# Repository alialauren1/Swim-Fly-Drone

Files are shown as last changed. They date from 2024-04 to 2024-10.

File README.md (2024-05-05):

# Swim Fly Drone Project

Our project entails constructing a submersible chamber capable of reaching
specified depths. The system will operate in a closed loop, maintaining control until it 
reaches a desired pressure depth.

This project was intended for our senior project where. Dr. Ghalamchi wants to improve previous tests on waterproof drones that can take off from underwater to allow for a drone that can float on top of the water surface as well as have added support to be pushed up from underwater. The new design needs to be detachable from the built waterproof drone to compare its new features in tests. The propellers must also be above the water surface when the drone is idling on the water so that the efficiency of takeoff can be compared to the drone without the chamber in which the whole drone is submerged underwater upon takeoff.

Our project for ME 405 will be the system attached to this drone, enabling the drone to submerge underwater with a minimum depth of 5ft. While allowing for the system to resurface and position the propellers above the water's surface. 

Pressure can be directly correlated to depth, given a liquid's density.
   In order to simulate this system for our ME 405 Term Project, this system takes a desired pressure setpoint and controls a motor-driven syringe system to
   pressurize a chamber to the setpoint. It waits a period of time, as if it were underwater collecting data,
   and then returns to the initial pressure, as if it were returning to the water surface. 

## Hardware design
In Figure 1, we can see the internal system of the system. We have integrated Ametck Pittman's PG6712A077-R3 motor to a 50 CC syringe. Utilizing this motor, we've have attached a worm gear and gears to ensure sufficient torque to be generated. These gears are attached to a pinion
and aligned with a rack that allows for the syringe to be moved back and forth. This allows
for the system to achieve the desired weight to submerge the whole system.

The gears were selected from McMaster. This is so in the future, they can be ordered parts. For now, we used the CAD files to 3D print them for budget reasons. While sizing and choosing the number of teeth we would need for our system, we calculated to torque that the motor needed to have to overcome the friction force between the piston and syringe. This calculation is shown below. In the future, we can order a motor that is more selectively chosen using this information. However for now, we used the motor provided to us in lab. 

$F_r = T_A / R_A$

$T_A = F_R * R_A$

$T_B = T_A$

$T_C = (N_C / N_B ) * T_B$

$T_C = (N_C / N_B ) * (F_R * R_A)$

$T_C = (1/15) * (6 N) * (.0152 m)$

$T_C = (0.006 Nm) = (6 mNm)$ 

Doing these calculations led us to select appropriate gears for our system, ensuring that they can withstand the pressure encountered during operation while maintaining an ideal speed. Below shows a table of the parameters.  

| **Parameters** | Variable | Value | Units |
|:---:|:---:|:---:|:---:|
| **----Rack+Piston+Syringe--** |  **-------** |  **----** |  **----** |
| Force to overcome friction in tube | F_R | 6 | N |
| **----Gears--** |  **-------** | **-----** | **-----** |
| Radius Gear A | R_A | 0.0152  | m |
| Teeth Gear A | N_A | 17 | |
| Outer Diameter Worm Gear B | OD_B | 16 | mm |
| Teeth Worm Gear B | N_B | 15 | |
| Pressure Angle Worm Gear B | Phi_C | 20 |  degrees  |
| Outer Diameter Worm C | OD_C | 12 | mm |
| Pressure Angle Worm C | Phi_C | 20 |  degrees  |
| Teeth Worm C | N_C | 1 | |
| **-----Motor Parameters------**  | **--------** | **-----** |  **----** |
| Radius of Motor Gear | rm |  0.00662  | m |
| Motor Nominal Voltage | V_DC | 12 | V |



Figure 1. CAD: Internal system of our terms project with labels indicating parts of the system.



Figure 2. CAD: Secondary view of the internal system of our terms project with labels indicating parts of the system.

Screenshot 2024-03-19 at 6 15 07 PM

Figure 3. Gears, motor, and frame for the internal system.

The pressure sensor we selected is the SSCMANV030PA2A3 Honeywell Pressure Sensor. It measures absolute pressure, with a range from 0-30 psi. Is allows liquid media on the port, which will come of use in future quarters when we test our system underwater. 

Screenshot 2024-03-19 at 8 53 00 PM

Figure 4. SSCMANV030PA2A3 Honeywell Pressure Sensor



Figure 5. Hardware all connected



Figure 6A. System Connected to Bottom of Drone Body - View 1



Figure 6B. System Connected to Bottom of Drone Body - View 2

Screenshot 2024-03-19 at 8 43 37 PM

Figure 7. Overall View of Drone Body with Chamber 

### Schematic

The schematic below shows a very general diagram of how components are being powered and communicating with one another. 
The power supply provides power to the motor. The power supply was set to 12V with a 0.5 A current limit. 

Schematic

Figure 8. Schematic of components

## Software design
The main program uses three classes inside two tasks that multitask with one another. A detailed description of the software design can be found on our doxygen main page linked here: 
https://alialauren1.github.io/ME405-Term-Project/index.html#soft_org_sec

To measure pressure, we used a Honeywell Board Mount Pressure Sensor, which uses I^2C communication. A class was made to use this sensor. Details on how the data was collected and process is linked below. Pressure Sensor: SSCMANV030PA2A3
https://alialauren1.github.io/ME405-Term-Project/index.html#autotoc_md1

Attaching the sensor and the Ametek motor to our Nucleo, we were able to program both components to get a functioning product.

### Tasks and States
The Tasks and States used in the main program are shown in diagrams linked on the page below.
https://alialauren1.github.io/ME405-Term-Project/index.html#T_S_sec

## Testing and Results

### Preliminary
Our senior project requires our chamber to be able to acheive at minimum, 5 ft depth. Calculations were run, shown below, to determine the pressure that coincides with a depth of 5 ft in water. Being a little under 16.5 psi, we decided to run initial tests at 16.5 psi.

Screenshot 2024-03-19 at 9 05 30 PM

In order to test our project sensors and motor control, we ran multiple tests in order to find our optimal Kp value. The results are presented in the plot down below. This was preliminary testing. 

Screenshot 2024-03-17 at 10 32 32 PM

Figure 9. Plot of Pressure vs Time inside the syringe. Each line represents a different run of data collected while altering the Kp value.

During our testing, we initially set Kp to 5 (shown in blue) and then increased it to 10 (shown in orange). Observing the graph, it's evident that increasing the Kp value led to faster attainment of the target pressure of 16.5 [psi].

While testing to achieve for efficiency in reaching the desired pressure, it's essential to consider what our system will be attached to. Our system with the syringe and pressure sensor will be attached to a drone. Rapid pressure and volume changes may introduce a moment within the drone body, causing the drone to loose control. Therefore, we must weigh the trade-offs between achieving rapid pressure targets and maintaining system stability.

As we continue to test our project, further tests will be necessary to determine the optimal balance between speed, the system stability and accuracy. This process may involve fine-tuning parameters beyond just changing the Kp. This may incude making the chamber of the system bigger and other factors.

### Lab Demo Results and Functionality of Product
The below plot shows the pressure inside the syringe. The autonomous journey is one in which the system reaches the desired setpoint, waits for a duration, and then returns to the initial pressure. 



Figure 10. Plot of Pressure vs Time inside the syringe with a setpoint of 17 [psi].  

This journey mimics future developement of our larger senior project in which this pressure chamber will be attached to a drone. We anticipate it will be beneficial for some remote or signal to send a desired depth as the setpoint to the system, in which the chamber will submerge with the drone, going to that depth. It will remain there, possible to collect data, and then autonomously return to the surface. 
We are satisfied with the final results. The chamber is able to reach pressures higher than a pressure corresponding to 5ft, which was what we wanted to achieve.
It is also able to maintain the increase in pressure while the motor is turned off, which is a satisfying result. 

The system also works at lower than atmosphere pressures. In the plot below, the setpoint was chosen as 13 psi. However, in another test, we were able run the system with an even lower setpoint of 10 psi. Although this is less necessary to have, it is satisfying to see that ability. 

Screenshot 2024-03-19 at 8 38 33 PM

Figure 11. Plot of Pressure vs Time inside the syringe with a setpoint of 13 [psi].  

## What we have learned
Designing this system taught us how important it is to design and test early. 
Although most of the system was done with a reasonable amount of time, we were faced with issues causing the system to take longer to complete than anticipated.

### 3D Printing
While 3D printing gears and housing system for our project we learned that tolerances while creating parts is harder to achieve. When 3D printing the gears it was harder to align the gears causing the small gears to slip and not allowing for our system to be as efficient as it can be.

Note: We are saving our used PLA parts to find a place to recycle them. 

Screenshot 2024-03-19 at 6 14 47 PM

Figure 12. Collection of gears tested

### Software and Sensors
We learned that the data being output from our pressure sensor was in counts. This led to the creation of a definition in our PressureSensor class to interpret the counts into a unit of measurement that could be easily interpretted, that being [psi]. Since our Closed-Loop Controller class uses the pressure sensor output in counts to correct for a desired pressure, an additional definition was made to interpret user desired setpoint input from [psi] to counts. 

## Safety
Our project prioritizes user safety through thoughtful design considerations. By utilizing small gears, we have effectively reduced the risk of injuries to the user. Once the system has been fully assembled, all moving components and electrical elements will be enclosed and inaccessible to the user. This design ensures that users are protected from potential hazards during the system's operation.

## Bugs and Future Work

We would also like to fix our code in Task2 State 3 where there is a break in data collection between the chamber resting at a higher pressure and then returning to its original pressure. As shown on the plot in the "Lab Demo Results" section, there is a small duration of time in which no data is collected. That is state 3, whilst counter_s3 is between 1 and 3. We tried removing this portion and only having state 3 reset the setpoint to initial pressure in one count but it did not initially work and we have run out of time to work on the code. So, for now, there is that small time duration blip in the data.  

In the future we would like to implement a third task into our main program that is a user interface for the pressure setpoint. 
The user could select from a range of setpoint options and the system would adjust the pressure in the chamber accordingly. 
This task would multitask with the other two tasks and allow for the user to input a setpoint whenever they want whilst the program runs. 

We plan to build a larger waterproof chamber to encompass components similar to those used in project. This will allows us to test the systems depth control abilities in actual water. We look forward to the continuation of this project and appreciate all that it has taught us so far. 

## Additional files

Pressure sensor datasheet:
[SSCMANV030PA2A3 Honeywell.pdf](https://github.com/alialauren1/ME405-Term-Project/files/14630972/SSCMANV030PA2A3.Honeywell.pdf)

I2C Communications with Honeywell Pressure Sensors:
[sps-siot-i2c-comms-digital-output-pressure-sensors-tn-008201-3-en-ciid-45841.pdf](https://github.com/alialauren1/ME405-Term-Project/files/14630975/sps-siot-i2c-comms-digital-output-pressure-sensors-tn-008201-3-en-ciid-45841.pdf)

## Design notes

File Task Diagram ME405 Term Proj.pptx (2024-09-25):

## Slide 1

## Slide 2

Initial Pressure
Bytes

Task 1 Print
Freq: 60 Hz
Priority: 1

Task 2 Get
Freq: 50 Hz
Priority: 2

Time and Pressure Bytes [100]

Task 2 State Status
Byte

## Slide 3

Task 2 Get

Start

setpoint_raw-6 <= reader_p_value <= setpoint_raw+6

counter_s3 == 4

State 2 Off
Collect Data whilst Motor Off

State 3 Go Back
Reset Setpoint to Initial Pressure

Always

State 1 Data
Collect Data and Run CL Controller

State 4 Nothing
Does nothing

counter == 20

(initialP-6 <= reader_p_value <= initialP+6)
& key == 1

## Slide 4

T2_state == 3

Task 1 Print

Start

T2_state == 1

State 2
No Values, Don’t Print

Always

State 1 Print
Print Values

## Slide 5

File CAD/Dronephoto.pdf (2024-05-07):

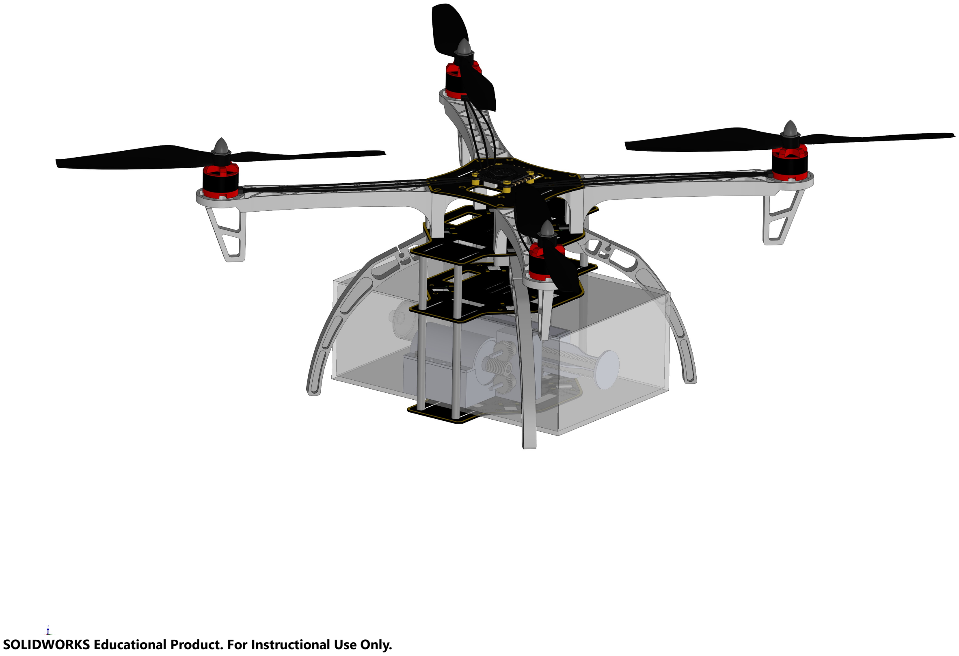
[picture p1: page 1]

SOLIDWORKS Educational Product. For Instructional Use Only.

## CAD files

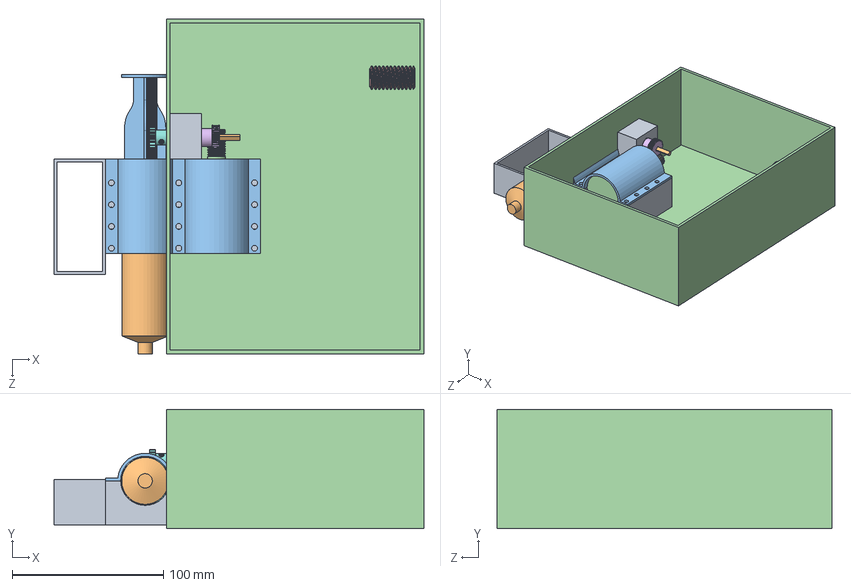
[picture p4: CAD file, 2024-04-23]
Pelican Paddler CAD/BuoyancyChamberAssembly_RevA.SLDASM
244.4 x 78.7 x 221.0 mm
ComponentStucture
60mlSyringeShell
60mlSyringePlunger
Motor_body
57545K736_Metal Worm Gear x 2
57545K624_Steel Worm
2664N437_Metal Gear - 20 Degree Pressure Angle x 2
2485N214_Metal Gear Rack - 20 Degree Pressure Angle x 2
6mm bar x 2

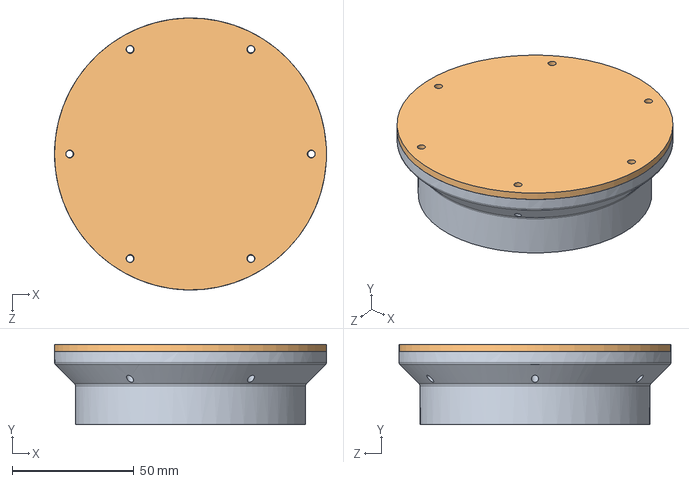
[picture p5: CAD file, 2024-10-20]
CAD/Housing/Housing Part Files/TestBox_LidSeal_v1.SLDASM
111.9 x 33.0 x 111.9 mm
TestBox_LidSeal_v1
TestBox_Lid_v1

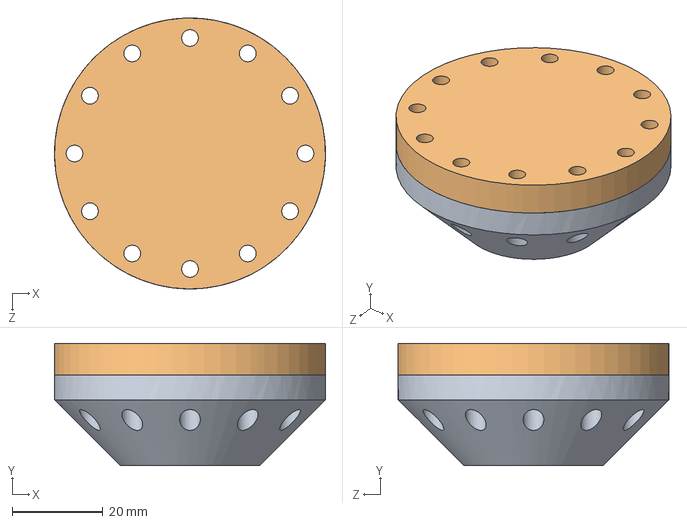
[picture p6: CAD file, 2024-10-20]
CAD/Housing/Housing Part Files/Lid Assembly.SLDASM
59.8 x 27.0 x 59.8 mm
TestBox_LidSeal_v1
Part1^Lid Assembly

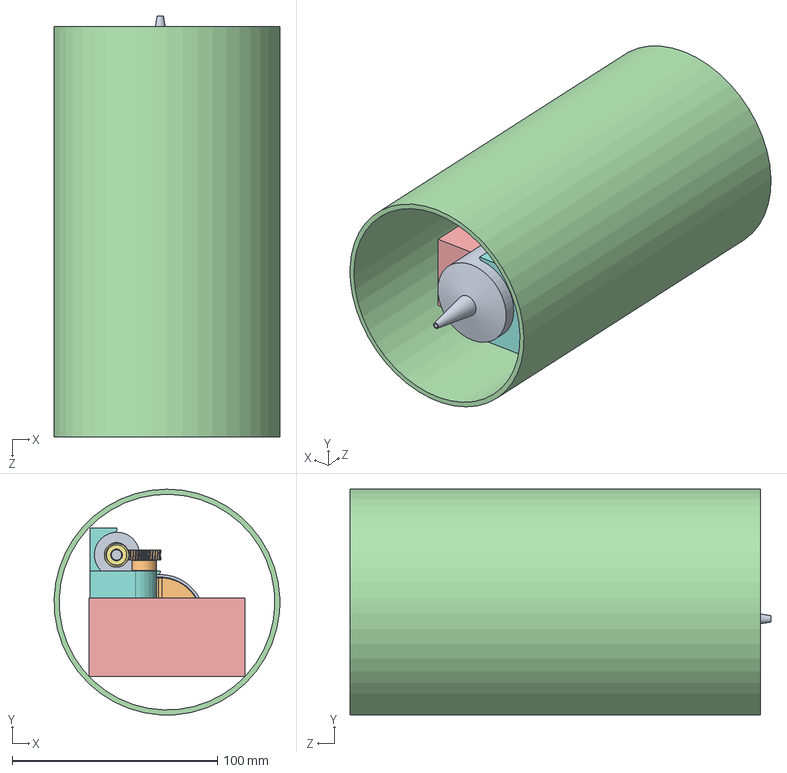
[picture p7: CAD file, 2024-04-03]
CAD/CAD_ME405/syring_1_V3.SLDASM
109.9 x 109.9 x 205.0 mm
syringe_out_1
syring_push_1
6mm bar
2664N411_Metal Gear - 20 Degree Pressure Angle
57545K624_Steel Worm
Motor_holder_V3
Motor_body
57545K737_Metal Worm Gear (1)
rack_V3

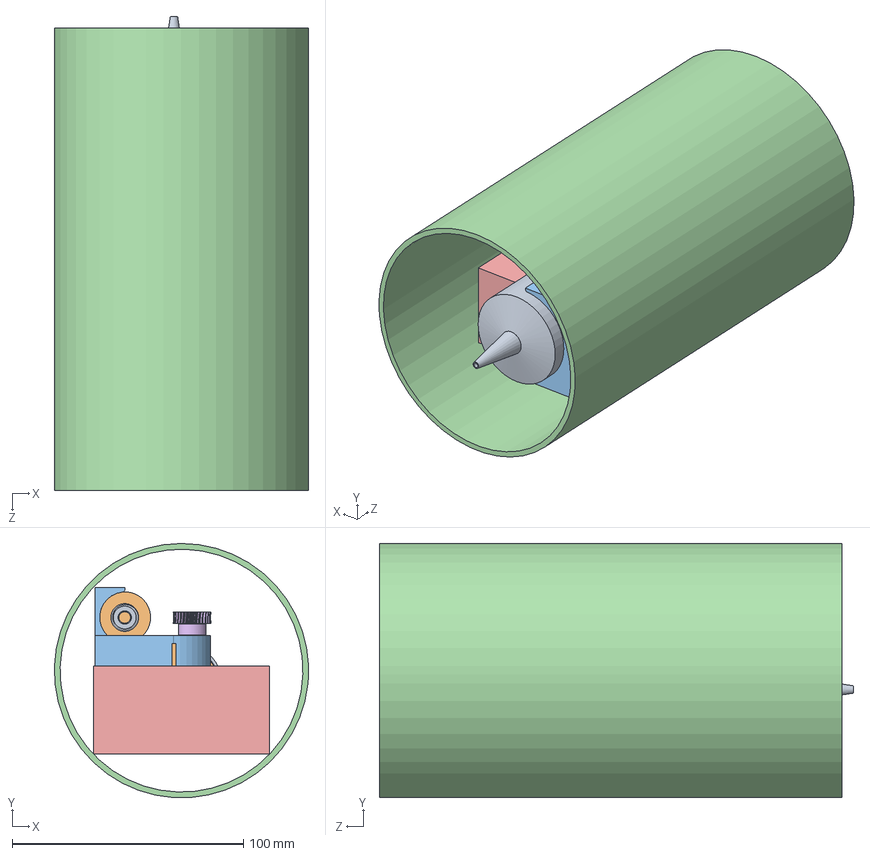
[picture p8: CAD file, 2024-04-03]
CAD/CAD_ME405/syring_1.SLDASM
109.9 x 109.9 x 205.0 mm
syringe_out_1
syring_push_1
6mm bar x 2
57545K737_Metal Worm Gear (1) x 2
2485N242_Metal Gear Rack - 20 Degree Pressure Angle x 2
2664N411_Metal Gear - 20 Degree Pressure Angle x 2
57545K624_Steel Worm
Motor_body
Motor_holder

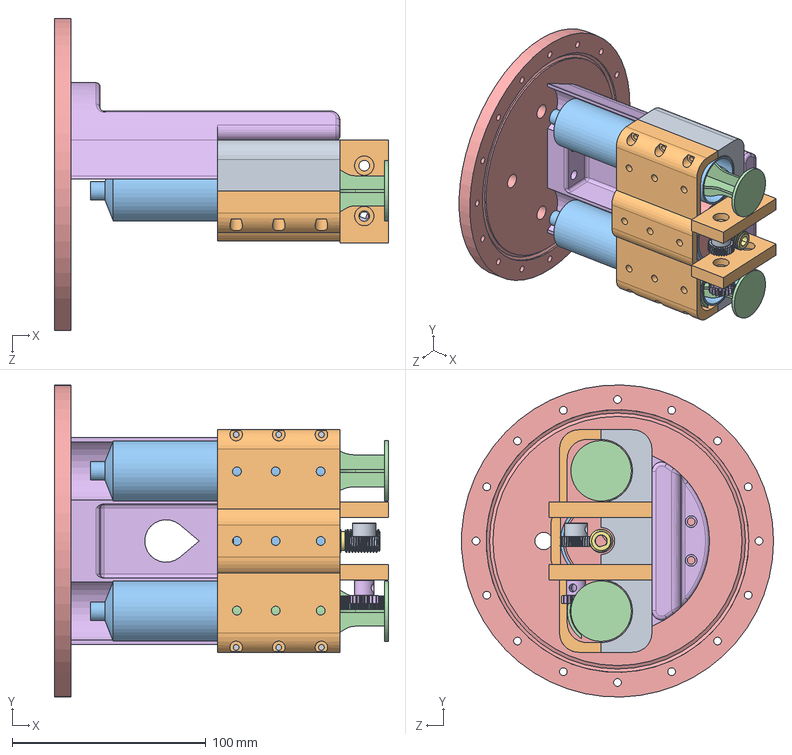
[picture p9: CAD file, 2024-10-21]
CAD/Bouyancy Chamber/dual syringe assembly.SLDASM
172.3 x 160.9 x 161.0 mm
ComponentStucture (dual sport)
Gear structure (dual sport) x 2
60mlSyringeShell x 2
60mlSyringePlunger x 2
Motor_body
2664N437_Metal Gear - 20 Degree Pressure Angle
57545K624_Steel Worm
2485N214_Metal Gear Rack - 20 Degree Pressure Angle
57545K736_Metal Worm Gear
Lid (dual sport)
motor spacer (dual syringe)
syringe spacer (dual syringe)
Bouynancy Chamber Housing Lid
Pump Attachment bracket (dual sport)

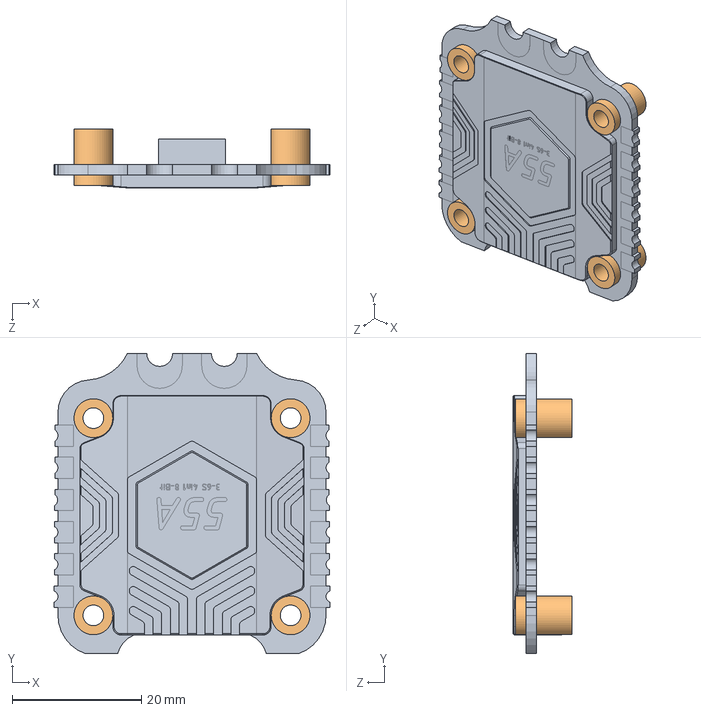
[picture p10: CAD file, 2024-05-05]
CAD/Done CAD SW22/ESC_Assembly.SLDASM
42.7 x 46.4 x 9.10 mm
spf455a 4in1 esc
fc7_g1 v1 x 4

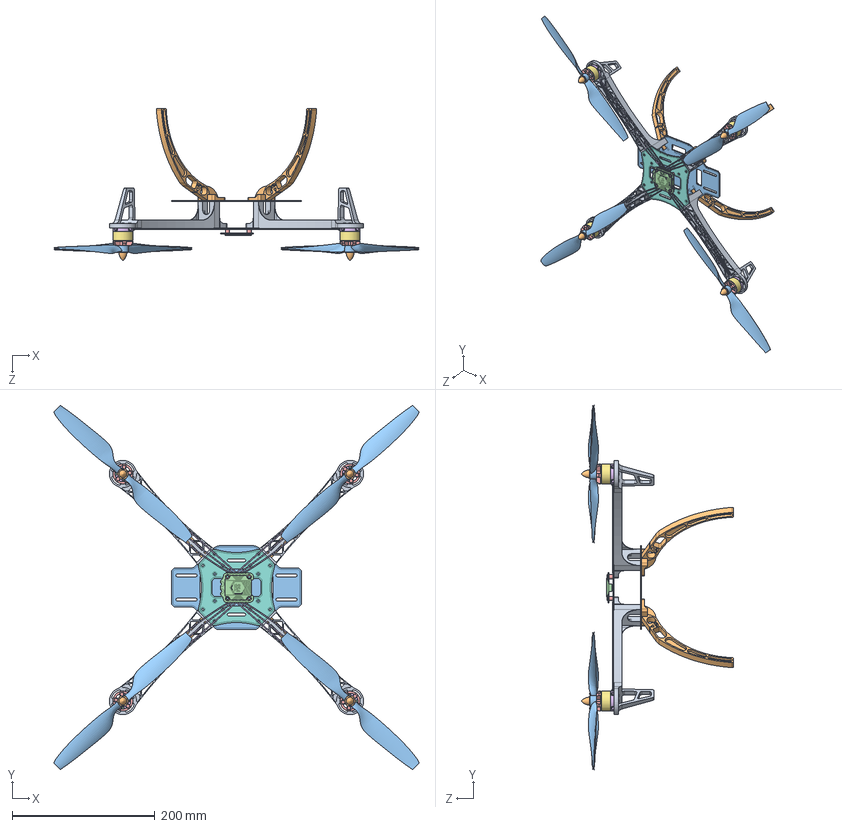
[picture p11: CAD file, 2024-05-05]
CAD/Done CAD SW22/Drone_Assembly.SLDASM
511.2 x 510.4 x 213.5 mm
Motor_input x 4
propeller_cap x 4
propellers x 4
Motor_bolts x 16
Top_motor x 4
bottom_motor x 4
middle_motor x 4
Top_Of_Drone_Frame
Drone_arm x 4
Drone_leg x 4
Bottom_of_drone_frame
spf455a 4in1 esc
fc7_g1 v1 x 4
wires x 4

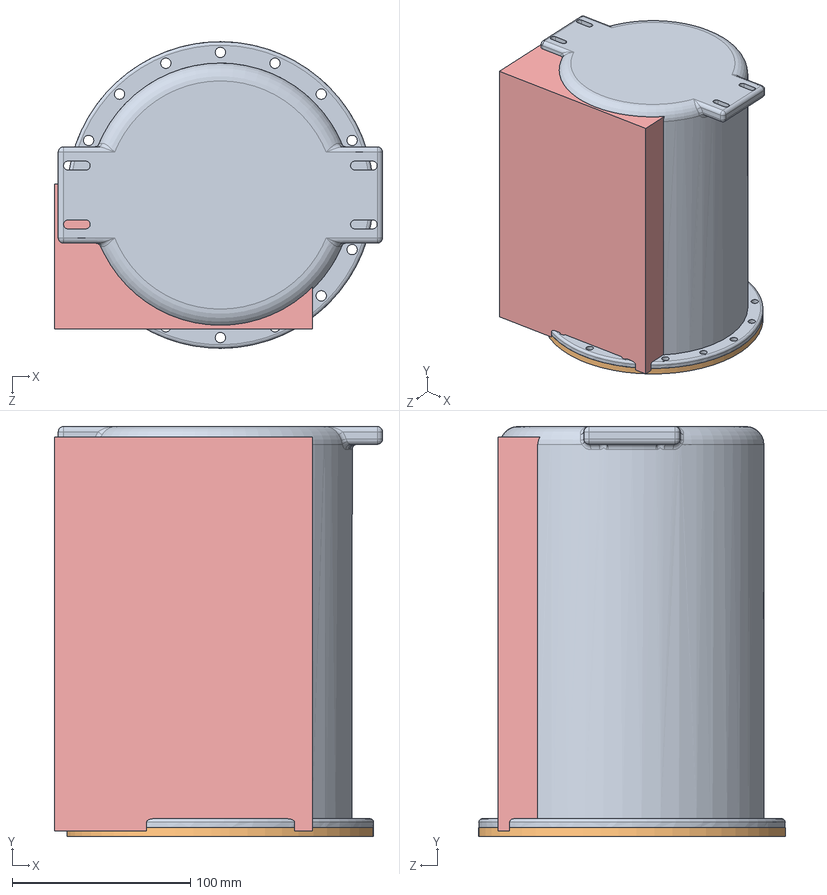
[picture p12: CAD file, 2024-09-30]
CAD/Bouyancy Chamber/Chamber System Assembly.SLDASM
184.1 x 230.0 x 172.0 mm
Bouynacy Chamber Housing
Bouynancy Chamber Housing Lid
ComponentStucture
60mlSyringeShell
60mlSyringePlunger
Motor_body
57545K624_Steel Worm
57545K736_Metal Worm Gear
2664N437_Metal Gear - 20 Degree Pressure Angle x 2
2485N214_Metal Gear Rack - 20 Degree Pressure Angle x 2
6mm bar x 2
MotorSyringeTopBracket

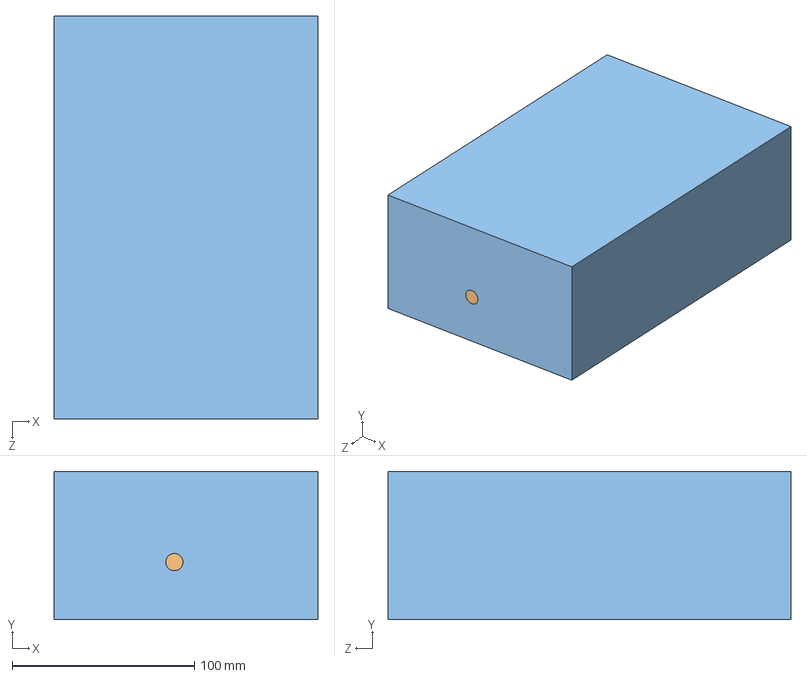
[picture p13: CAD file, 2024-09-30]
CAD/Bouyancy Chamber/BuoyancyChamberAssembly_RevA.SLDASM
144.8 x 81.3 x 221.0 mm
ComponentStucture
60mlSyringeShell
60mlSyringePlunger
Motor_body
57545K624_Steel Worm
57545K736_Metal Worm Gear
2664N437_Metal Gear - 20 Degree Pressure Angle x 2
2485N214_Metal Gear Rack - 20 Degree Pressure Angle x 2
6mm bar x 2
MotorSyringeTopBracket

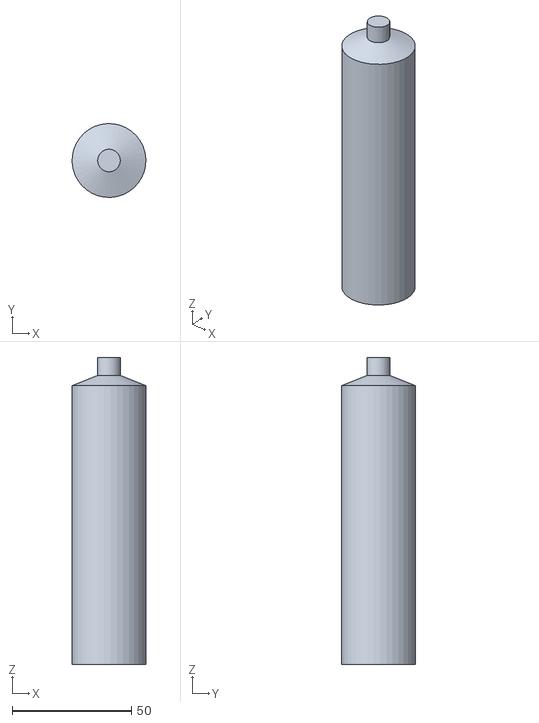
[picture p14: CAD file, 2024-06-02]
CAD/Bouyancy Chamber/BuoyancyChamberAssembly_RevA - 60mlSyringeShell-1.STL
31.0 x 31.0 x 128.8

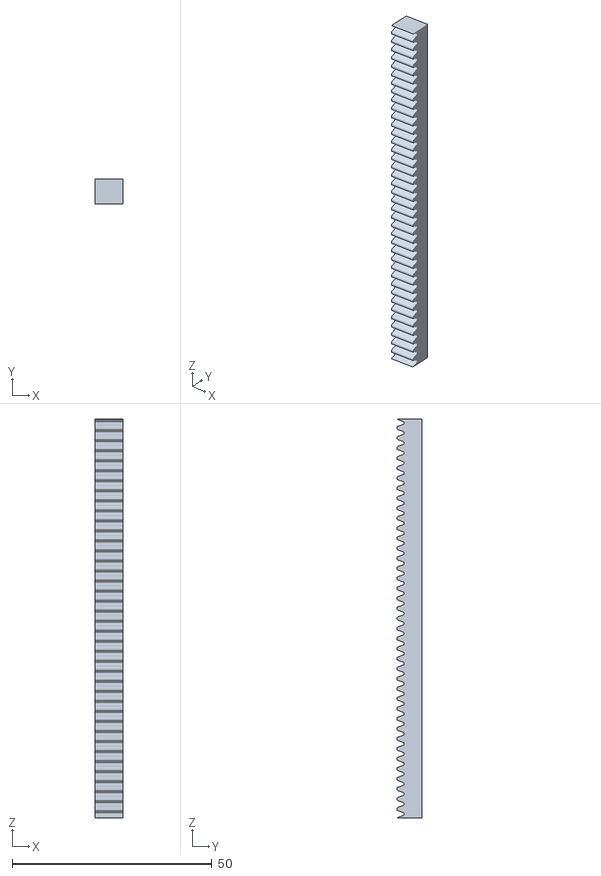
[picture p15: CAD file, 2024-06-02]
CAD/Bouyancy Chamber/BuoyancyChamberAssembly_RevA - 2485N214_Metal Gear Rack - 20 Degree Pressure Angle-3.STL
7.00 x 6.25 x 100.0

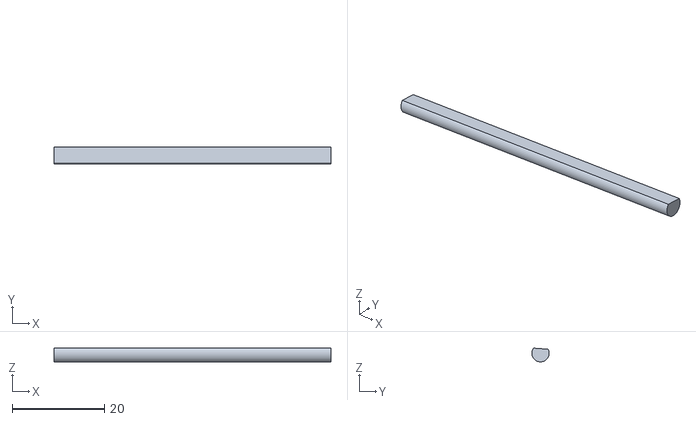
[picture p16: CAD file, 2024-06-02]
CAD/Bouyancy Chamber/BuoyancyChamberAssembly_RevA - 6mm bar-2.STL
60.0 x 3.75 x 3.00

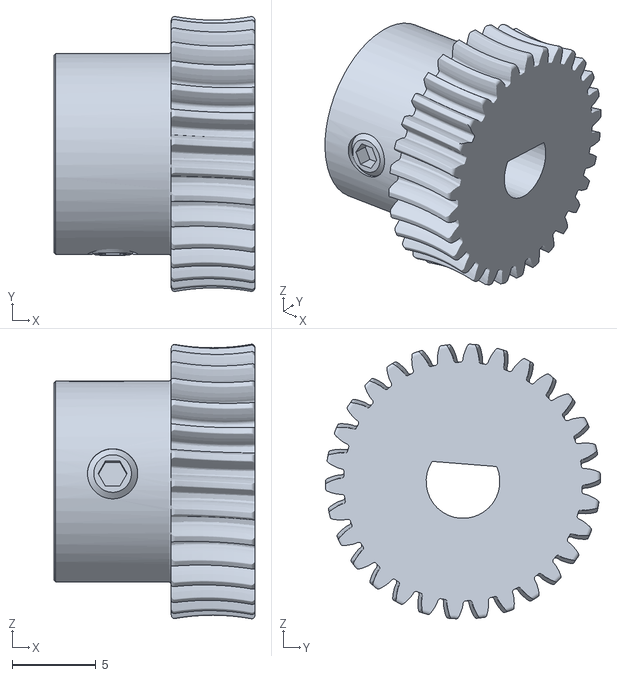
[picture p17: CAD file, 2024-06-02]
CAD/Bouyancy Chamber/BuoyancyChamberAssembly_RevA - 57545K736_Metal Worm Gear-2.STL
12.0 x 16.4 x 16.4

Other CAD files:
CAD/Drone CAD/Drone_Assembly.SLDASM
CAD/Drone_Body/Drone_body_V1.SLDASM
CAD/Drone CAD/SPBF4 V3 55A 4in1 ESC/ESC_Assembly.SLDASM
motor_testing/motor_testing stand.SLDASM
CAD/Bouyancy Chamber/2485N214_Metal Gear Rack - 20 Degree Pressure Angle.SLDPRT
CAD/Bouyancy Chamber/2664N437_Metal Gear - 20 Degree Pressure Angle.SLDPRT
CAD/Bouyancy Chamber/57545K624_Steel Worm.SLDPRT
CAD/Bouyancy Chamber/57545K736_Metal Worm Gear.SLDPRT
CAD/Bouyancy Chamber/60mlSyringePlunger.SLDPRT
CAD/Bouyancy Chamber/60mlSyringeShell.SLDPRT
CAD/Bouyancy Chamber/Bouyancy chamber (but it a box).SLDPRT
CAD/Bouyancy Chamber/Bouynacy Chamber Housing.SLDPRT
CAD/Bouyancy Chamber/Bouynancy Chamber Housing Lid.SLDPRT
CAD/Bouyancy Chamber/BuoyancyChamberAssembly_RevA - 2485N214_Metal Gear Rack - 20 Degree Pressure Angle-2.STL
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

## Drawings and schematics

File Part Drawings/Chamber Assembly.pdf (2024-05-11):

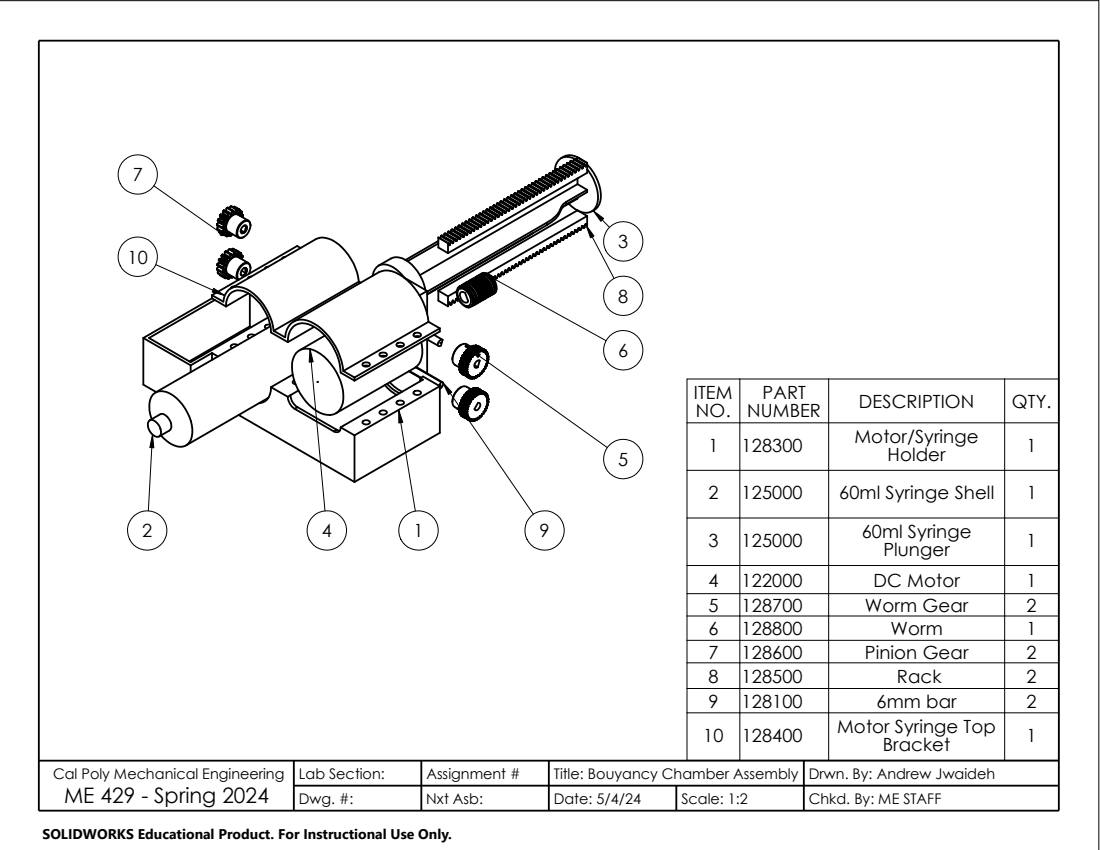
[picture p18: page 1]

ITEM NO. | PART NUMBER | DESCRIPTION | QTY.

1 | 128300 | Motor/Syringe Holder | 1

2 | 125000 | 60ml Syringe Shell | 1
3 | 125000 | 60ml Syringe Plunger | 1

4 | 122000 | DC Motor | 1
5 | 128700 | Worm Gear | 2
6 | 128800 | Worm | 1
7 | 128600 | Pinion Gear | 2
8 | 128500 | Rack | 2
9 | 128100 | 6mm bar | 2
10 | 128400 | Motor Syringe Top Bracket | 1

Cal Poly Mechanical Engineering ME 429 - Spring 2024 | Lab Section: | Assignment # | Title: Bouyancy Chamber Assembly | Drwn. By: Andrew Jwaideh
Dwg. #: | Nxt Asb: | Date: 5/4/24 | Scale: 1:2 | Chkd. By: ME STAFF

SOLIDWORKS Educational Product. For Instructional Use Only.

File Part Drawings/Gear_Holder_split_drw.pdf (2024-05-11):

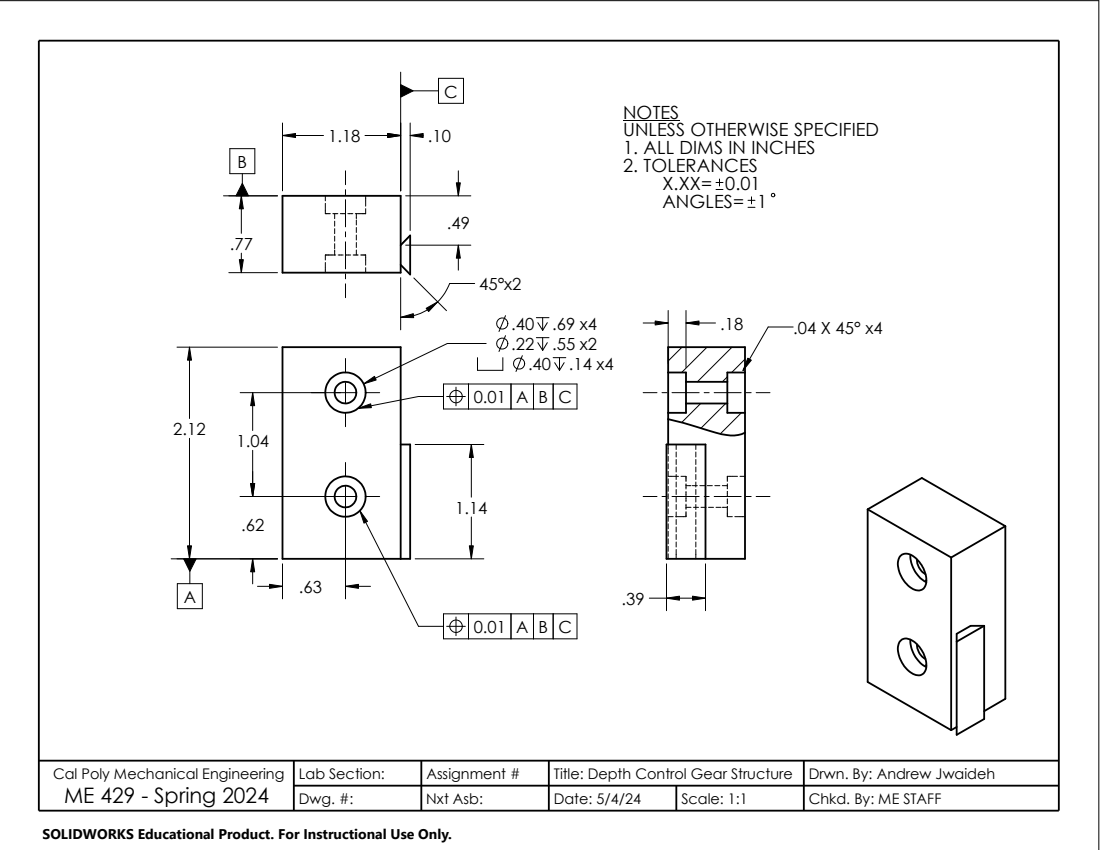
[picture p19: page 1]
ANGLES=

NOTES
UNLESS OTHERWISE SPECIFIED
1. ALL DIMS IN INCHES
2. TOLERANCES

Cal Poly Mechanical Engineering ME 429 - Spring 2024 | Lab Section: | Assignment # | Title: Depth Control Gear Structure | Drwn. By: Andrew Jwaideh
Dwg. #: | Nxt Asb: | | Scale: 1:1 | Chkd. By: ME STAFF Date: 5/4/24

SOLIDWORKS Educational Product. For Instructional Use Only.

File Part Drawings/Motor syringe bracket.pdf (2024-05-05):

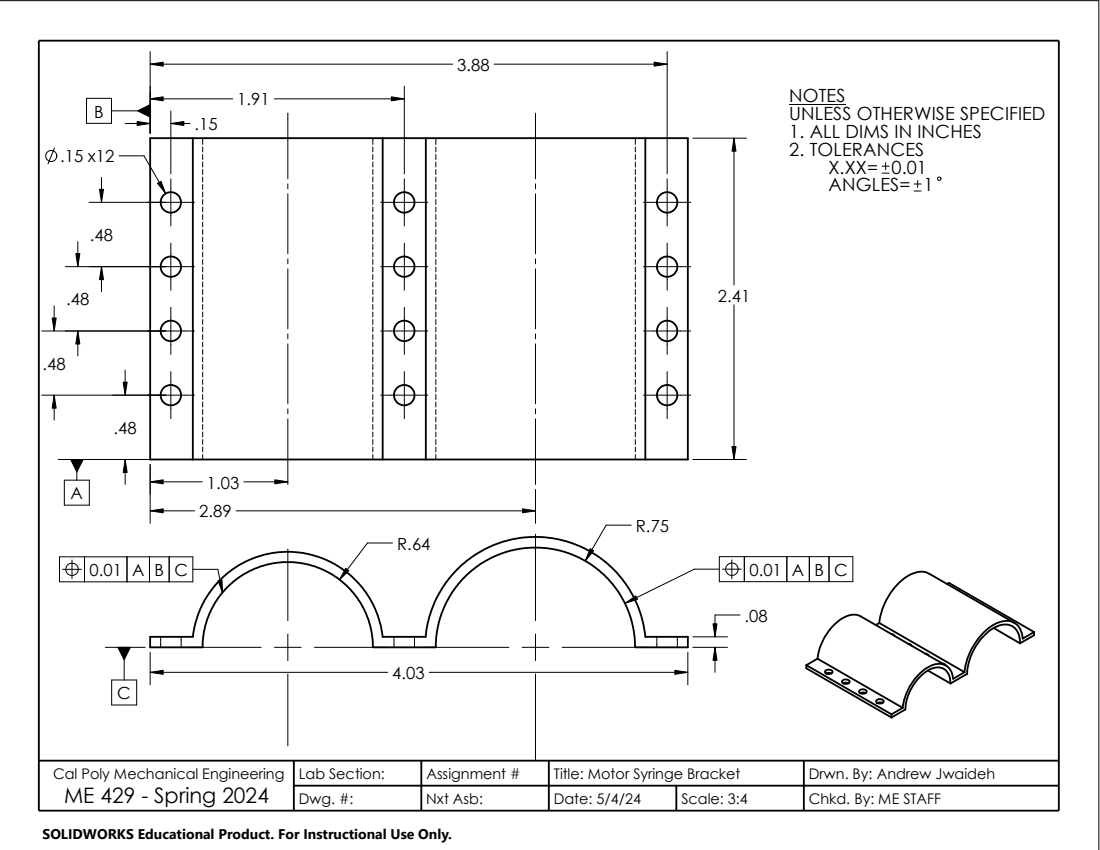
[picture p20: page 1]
ANGLES=

NOTES
UNLESS OTHERWISE SPECIFIED
1. ALL DIMS IN INCHES
2. TOLERANCES

Cal Poly Mechanical Engineering ME 429 - Spring 2024 | Lab Section: | Assignment # | Title: Motor Syringe Bracket | Drwn. By: Andrew Jwaideh
Dwg. #: | Nxt Asb: | Date: 5/4/24 | Scale: 3:4 | Chkd. By: ME STAFF

SOLIDWORKS Educational Product. For Instructional Use Only.

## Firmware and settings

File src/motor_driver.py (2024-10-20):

"""!
@file motor_driver.py
    This file is a class that implements a motor driver,
    setting the duty cycle for the motor.
    It allows for initialization of the chosen motor pins and timer.
  
@author Alia Wolken, Eduardo Santos, Andrew Jwaideh
@date   2024-March-15 
"""

import pyb
import time

class motordriver:
    """!
    This class implements a motor driver from our 405 kit. 
    @author Alia Wolken, Eduardo Santos, Andrew Jwaideh
    """

    def __init__ (self, en_pin, in1pin, in2pin, timer):
        """! 
        Creates a motor driver by initializing GPIO
        pins and turning off the motor for safety. 
        @param en_pin: enable pin
        @param in1pin: motor connected to this pin
        @param in2pin: motor connected to this pin
        @para timer: timer being used
        """
        # print ("Creating a motor driver")
        en_pin = pyb.Pin(en_pin, pyb.Pin.OUT_PP)
        en_pin.value(1)
        self.in1pin = pyb.Pin(in1pin, pyb.Pin.OUT_PP) # allows variable to be used across functions
        self.in2pin = pyb.Pin(in2pin, pyb.Pin.OUT_PP)

        tim2 = pyb.Timer(timer, freq=20000)
        self.ch1 = tim2.channel(1, pyb.Timer.PWM, pin=self.in1pin) # control motor direction
        self.ch2 = tim2.channel(2, pyb.Timer.PWM, pin=self.in2pin)


    def set_duty_cycle (self, level):
        """!
        This method sets the duty cycle to be sent
        to the motor to the given level. Positive values
        cause torque in one direction, negative values
        in the opposite direction.
        @param level A signed integer holding the duty
               cycle of the voltage sent to the motor 
        """
        # print (f"Setting duty cycle to {level}")
        # print(level)
        # if level positive
        if level > 0:
            self.ch1.pulse_width_percent(0)
            self.ch2.pulse_width_percent(level)
            
            # print("pos")
        # if level negative, make level positive, then do switch level and 0
        elif level  == 0:
            self.ch1.pulse_width_percent(0)
            self.ch2.pulse_width_percent(0)
            #print("zero")
        else:
            evel_abs = abs(level)
            # print(level)
            self.ch1.pulse_width_percent(evel_abs)
            self.ch2.pulse_width_percent(0)
            #print("negative")
            
def loop_example():
    
    # initialize button and pins needed for it
    HOT_pin = pyb.Pin(pyb.Pin.board.PB10, pyb.Pin.OUT_PP)
    LOW_pin = pyb.Pin(pyb.Pin.board.PB10, pyb.Pin.OUT_PP)
    # HOT_pin.value(1) # make it high???
    
    # do while loop where if button high or if flag is high, run motor inside loop
    
    # do while loop where while the button is say high, run motor.
    # button will not be high until pressed
    
    print("in test loop")
    moe.set_duty_cycle(70) # + to close, - to open plunger (as in pull water in)
    time.sleep(3)
    moe.set_duty_cycle(0)
    time.sleep(1)
            
if __name__ == '__main__':
               
   # moe = motordriver (pyb.Pin.board.PC1, pyb.Pin.board.PB4, pyb.Pin.board.PB5, 3)
    moe = motordriver (pyb.Pin.board.PB10, pyb.Pin.board.PB4, pyb.Pin.board.PB5, 3)
    loop_example()
            
#     while True:    
#         moe.set_duty_cycle (50)
#         time.sleep(1)

    
    # Wait for a certain duration (e.g., 5 seconds)
    # pyb.delay(5000)  # 5000 milliseconds = 5 seconds
 

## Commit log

2024-04-03 files from term project copied onto here
    [2485N236_Metal Gear Rack - 20 Degree Pressure Angle.SLDPRT, 2485N242_Metal Gear Rack - 20 Degree Pressure Angle.SLDPRT, 2485N242_Metal Gear Rack - 20 Degree Pr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]
2024-04-09 Drone body, Motor, Propellers CAD
    [Bottom_of_drone_frame.SLDPRT, Drone_arm.SLDPRT, Drone_body_V1.SLDASM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]
2024-04-14 CAD Updates
    Updated CAD model to be parametric
    added mechanical mates
    [2485N214_Metal Gear Rack - 20 Degree Pressure Angle.SLDPRT, 2664N437_Metal Gear - 20 Degree Pressure Angle.SLDPRT, 57545K624_Steel Worm.SLDPRT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]
2024-04-16 CAD Updates
    [BuoyancyChamberAssembly_RevA.SLDASM, ComponentStucture - 2485N214_Metal Gear Rack - 20 Degree Pressure Angle-2.STL, ComponentStucture - 2485N214_Metal Gear Rac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]
2024-04-18 Motor CAD
    [motor test.SLDPRT, motor_test_cap.SLDPRT, motor_testing stand.SLDASM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]
2024-04-19 STEP files for CAD
    [motor test.STEP, motor_test_cap.STEP, motor_testing stand.STEP]
2024-04-19 Update .70 to .62inches
    [motor test.SLDPRT]
2024-04-23 motor testing stand update
    [motor test stand.SLDPRT, motor test.SLDPRT, motor_test_cap.SLDPRT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]
2024-04-23 Motor test update
    [motor test.SLDPRT, motor test_test_v3.SLDPRT, motor_test_cap.SLDPRT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]
2024-04-23 STL motor_test
    [motor test_test_v3.SLDPRT, motor test_test_v3.STL]
2024-04-23 Motor testing CAD update
    [motor test_test_v3.SLDPRT, motor test_test_v4.STL, motor_test_cap_4bar.SLDPRT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]
2024-04-23 updates to cad
    [BuoyancyChamberAssembly_RevA.SLDASM, ComponentStucture - 2485N214_Metal Gear Rack - 20 Degree Pressure Angle-2.STL, ComponentStucture - 2485N214_Metal Gear Rac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]
2024-04-24 Cad update
    [motor_test_cap_4bar.SLDPRT, motor_test_cap_V2.SLDPRT]
2024-04-24 STP of update
    [motor_test_cap_4bar.STL]
2024-04-25 Botttom cap
    [motor_test_cap_4bar_bottom_part.SLDPRT, motor_test_cap_4bar_bottom_part.STL]
2024-04-25 motor stand v6
    [motor test_test_v3.SLDPRT, motor test_test_v5.STL, motor test_test_v6.STL]
2024-04-25 Updates 4.25.24
    [motor test_test_v3.SLDPRT, motor_test_cap_4bar.SLDPRT, motor_test_cap_4bar_bottom_V2.SLDPRT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]
2024-05-03 added notes to pressure sensor code
2024-05-05 Drawings Added
    [BuoyancyChamberAssembly_RevA.SLDDRW, ComponentStucture.SLDPRT, Gear_Holder.SLDDRW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]
2024-05-05 Reorganized files
    [Bottom_of_drone_frame.SLDPRT, BuoyancyChamberAssembly_RevA.SLDDRW, Drone_Assembly.SLDASM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]
2024-05-05 Attached chamber to drone
    [ComponentStucture.SLDPRT, TupperWare.SLDPRT]
2024-05-05 Drone Assembly with chamber
    [Base PCB.SLDPRT, Holybro GPS.SLDPRT]
2024-05-07 added parts
    [91290A172_Alloy Steel Socket Head Screw.SLDPRT, 93265A036_Female Threaded Round Standoff.SLDPRT, 93265A473_Female Threaded Round Standoff.SLDPRT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]
2024-05-09 Wi-Fi Antenna and GPS module
    [Base PCB.SLDPRT, Holybro GPS.SLDPRT]
2024-05-11 Updated Full Drone Assembly&Drawing
    [95412A415_18-8 Stainless Steel Threaded Rod.SLDPRT, Base PCB.SLDPRT, Drone_Assembly_RevC.SLDDRW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]
2024-05-11 Drawing updates
    [BuoyancyChamberAssembly_RevA.SLDDRW, Gear_Holder_split_drw.SLDDRW]
2024-05-23 different PWMs
2024-09-25 New Motor Driver Configured
2024-09-25 Updated motor pins & date
2024-09-29 Waterproofing Test Boxes
    [Drone_arm.SLDPRT, Motor_bolts.SLDPRT, Motor_input.SLDPRT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]
2024-09-29 Chamber Cylinder Design
    CAD for a potential chamber design.
    [Bouynacy Chamber Housing.SLDPRT, Bouynancy Chamber Housing Lid.SLDPRT, BuoyancyChamberAssembly_RevA.SLDASM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]
2024-09-30 UPDATED CHAMBER
    [Bouynacy Chamber Housing.SLDPRT, Bouynancy Chamber Housing Lid.SLDPRT, BuoyancyChamberAssembly_RevA.SLDASM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]
2024-09-30 Update Bouynancy Chamber Housing Lid.SLDPRT
    [Bouynancy Chamber Housing Lid.SLDPRT]
2024-10-01 Housing Test Prints 9/30/2024
    [TestBox_LidSeal_TenPercentComp_v2.STL, TestBox_LidSeal_TwentyFivePercentComp_v2.STL, TestBox_LidSeal_v1.SLDASM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]
2024-10-20 Dual sport version 1
    [2664N437_Metal Gear - 20 Degree Pressure Angle.SLDPRT, 57545K624_Steel Worm.SLDPRT, 57545K736_Metal Worm Gear.SLDPRT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]
2024-10-20 adding button to motor driver test
    [2485N242_Metal Gear Rack - 20 Degree Pressure Angle.3mf]
2024-10-20 updates to dual sport
    [Gear structure (dual sport).SLDPRT, Gear structure (dual sport).STEP, dual syringe assembly.SLDASM]
2024-10-20 dual sport l bracket holes
    [ComponentStucture (dual sport).SLDPRT, ComponentStucture (dual sport).STEP, dual syringe assembly.SLDASM]
2024-10-21 Chamber holder
    [Bouynancy Chamber Housing Lid.SLDPRT, ComponentStucture (dual sport).SLDPRT, Pump Attachment bracket (dual sport).SLDPRT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]
2024-10-24 update to dovetail
    [Gear structure v3 (dual sport).STEP]
